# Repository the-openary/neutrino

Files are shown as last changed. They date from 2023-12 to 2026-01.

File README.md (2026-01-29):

# Neutrino

### Overview

This is Neutrino! It's a portable 3D printer that is meant to be cheap and accessible - it fits inside a filament box! ~~Currently in development~~ currently unfinished, do NOT try building your own without messaging me for help for now. Join the the Discord server [here!](https://discord.gg/VZFWGp7FHZ). Made by @qcoral

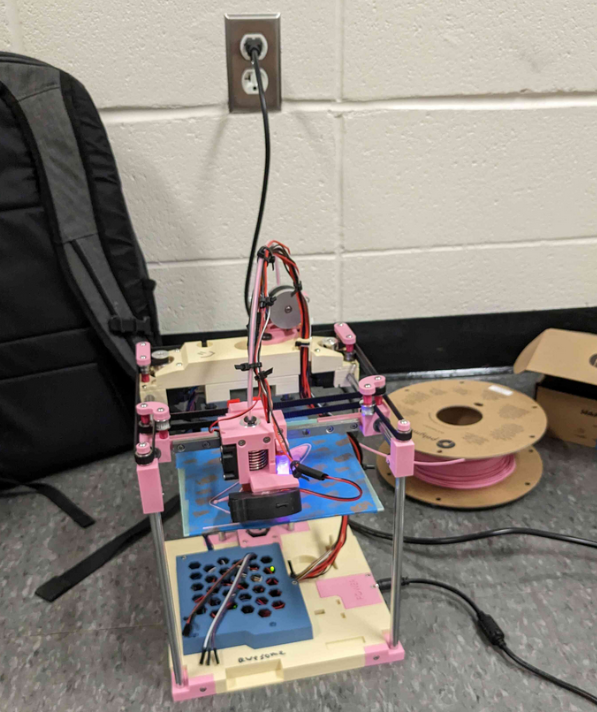
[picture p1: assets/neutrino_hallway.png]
Picture of Neutrino in a hallway


The `dev_process` folder contains a selection of notes & data that provide a peek into the development process of this printer. Due to privacy reasons it is only a snippet. If there's something specific feel free to reach out. 

### Features
- Fits in a 200x200x70mm volume
- Under $300 CAD (using the attached BOM)
- Uses common, off-the-shelf parts
- Mostly self replicating

*currently the base cannot be self-printed

## 2025-12-12 Update:

I last updated this printer almost 2 years ago in 2024. The printer works, but the useability could definitely be improved.

While I would love to someday really put in the polish to properly finish this design, I really am not sure when that would be. Many of the parts would have to be redesigned from scratch, and I've recently been enjoying other projects much more. That being said, this was still an absolute blast to work on!

Feel free to fork this if you so desire. All I ask is that you give proper attribution!

---
### Getting started

In the root of the repository is a file called `BOM.xlsx`. Contains all the relevant links, notes, etc. Currently missing screw counts, please use the CAD for that!

Join the discord for help, I will gladly give guidance on how to build your own.

---
### FAQ:

**Can I see a video?**

There are short clips that can be found in the discord. Currently working on a proper release video, will try and get that out soon<sup>tm</sup>.

**Where's the extruder?**

Great question! Neutrino is designed to use a Sherpa Mini in bowden configuration. Due to copyright, it cannot be included in the CAD. It can be found [here](https://github.com/Annex-Engineering/Sherpa_Mini-Extruder). Totally awesome design.

**Why a Bowden Setup?**

Initially the printer had a Direct Drive setup, but this was later swapped to Bowden. There were a couple reasons for this
- Faster printing
- Short tube length
- Easier maintenance
- Easier to explain to others
    - Being a portable printer, many people who have never seen a 3D printer see it. I think this makes Neutrino double as an educational/inspirational tool and for that reason it is easier to explain the separate parts of a Bowden extruder vs a DD setup. 

**Where can I source my parts?**

Anywhere you can find them. The `BOM.xlsx` file contains links to all the sources that I used during development. The printer itself uses all standard 8mm + M3 hardware. Use AliExpress, Amazon, spare parts, etc. Unfortunately you will need to print your own parts for now, but that will change soon.

**Is there an assembly guide?**

Not yet, working on that soon. For now you should just use the CAD. There is also the [discord](https://discord.gg/VZFWGp7FHZ) for help. I can assist you personally there.

**What is under `OLED_Module`?**

Under OLED_Module is a custom, optional PCB that contains an OLED display, rotary encoder, kill switch, and speaker. The case is still WIP, but the PCB itself has been tested and works well.

**Why the name "Neutrino"?**

The [Positron](https://github.com/KRALYN/PositronV3) project was a huge inspiration for me whilst designing this project. Seeing the innovation process and Kralyn's willingness to tackle problems was a huge motivator for me. While Neutrino was originally a codename, I believe it fits pretty well. 

---

### TODO:

- [ ] Make the base self replicating
- [ ] Misc clearance fixes
- [ ] Add pin breakout connector
- [ ] Add PET Recycling integration

#### [Credits](/CREDITS.md)

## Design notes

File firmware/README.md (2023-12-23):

## Firmware Configuration

ESP8266 & Klipper firmware for Neutrino

In the esp8266 folder there is a precompiled hex file for the Wemos D1 Mini. The credentials are preconfigured to the following:
- SSID: esp@neutrino
- Password: secretpi

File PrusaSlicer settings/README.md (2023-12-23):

# PrusaSlicer Settings

Config files for PrusaSlicer. Currently contains the printer settings and profiles for:

Layer heights:
- 0.3mm
- 0.2mm

Filaments:
- PLA

More to be added soon. Currently one large file, working on separating each profile so you can import only what you need. Refer to [PrusaSlicer Documentation](https://help.prusa3d.com/article/how-to-import-and-export-custom-profiles-in-prusaslicer_382766) for help.

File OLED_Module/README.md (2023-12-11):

Custom OLED Module for the Neutrino

Pinout for SKR Mini E3 V2.0

```
 *            SKR Mini E3 V2.0
 *                 ------
 * (NONE)    PB5  | 1  2 | PA15 (BTN_ENC)
 * (BTN_EN1) PA9  | 3  4 | RESET
 * (BTN_EN2) PA10   5  6 | PB9  (SDA)
 * (SCL)     PB8  | 7  8 | PB15 (BEEPER)
 *            GND | 9 10 | 5V
 *                 ------
 *                  EXP1
 ```
Source: https://upload.wikimedia.org/wikipedia/commons/9/90/Stm32f103_pinout_diagram.png

Editing Marlin: 
- Add the following to `pins_BTT_SKR_MINI_E3_common.h` under  `#elif HAS_WIRED_LCD`
```C
  #elif ENABLED(OLED_PANEL_TINYBOY2)

    #define BEEPER_PIN EXP1_08_PIN //PB15

    #define BTN_ENC EXP1_02_PIN //PA15
    #define BTN_EN1 EXP1_03_PIN //PA9
    #define BTN_EN2 EXP1_05_PIN //PA10
```
- Then select 
```C 
#define OLED_PANEL_TINYBOY2
``` 
Under the `OLED Displays` section of `configuration.h` (roughly line 2980)

Special thanks to czupryna011 for the instructable I based this off of https://www.instructables.com/Small-and-Cheap-Tiny-OLED-for-Ender-3-stock-and-SK/

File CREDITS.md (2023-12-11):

# Credits

The CAD model uses the following models as placeholders for now:

- [Raspberry Pi Zero W](https://grabcad.com/library/raspberry-zero-1)
- [BLTouch](https://grabcad.com/library/bltouch-v3-1-1)
- [Lolin D1 Mini](https://grabcad.com/library/wemos-esp8266-lolin-d1-mini-v4-1)
- As well as an SKR Mini & E3D v6 from the VORON Project 3D printer CAD files

These models were very useful during the design process off the printer, particularly when mapping out locations of the different parts. These will be replaced by custom-made models in the future, but for now these models are used

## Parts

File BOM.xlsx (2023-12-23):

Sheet: Main Parts
Item | Quantity | Main Price | Alt. Price | Link | Notes | Alternative source | Alternate source 2
KINEMATICS
STEPPERONLINE NEMA 17 20mm motor 3pcs | 1 | $41.47 |  | https://www.aliexpress.com/item/1005003226027617.html | Alternative source has JST connectors | https://www.aliexpress.com/item/1005004708155105.html | https://www.aliexpress.com/item/32585429251.html
MGN9C Linear Rail 150mm (LYXCNC) | 1 | $10.14 |  | https://www.aliexpress.com/item/1005004519572683.html
4pcs 8x150mm linear rod (ZHUHAI) | 1 | $14.06 |  | https://www.aliexpress.com/item/1005001813564948.html | For Z axis, you can optionally do 200mm. Make sure to change leadscrew accordingly!
2pcs 8x150mm linear rod (ZHUHAI) [Y Axis] | 1 | $8.48 |  | https://www.aliexpress.com/item/1005001585997299.html | For Y axis, do not change!
2PCs LM8SUU (SUPER3D) | 1 | $2.91 |  | https://www.aliexpress.com/item/32819163985.html
1PCs LM8UU (SUPER3D) | 2 | $3.52 |  | https://www.aliexpress.com/item/4000528511830.html
GT2 2GT Open Belt 3m (POWGE) | 1 | $8.45 |  | https://www.aliexpress.com/item/902692789.html
1pcs 150mm 2mm pitch 8mm leadscrew (ZHUHAI) | 1 | $6.55 |  | https://www.aliexpress.com/item/32873975375.html | Alternate source $3.67 | https://www.aliexpress.com/item/4001332632943.html
10pcs F623ZZ Bearing (AXK HARDWARE) | 2 | $9.48 |  | https://www.aliexpress.com/item/1005002679059125.html | Alternate source is roughly $15, RS. Can use toothed idler pulleys, we just need 12 "Joints" total. | https://www.aliexpress.com/item/1005004095001000.html
1pcs GT2 2GT 5MM Bore Timing pulley (POWGE) | 2 | $7.05 |  | https://www.aliexpress.com/item/32995102911.html | Alternate source is roughly $2.34, quality could be suspect | https://www.aliexpress.com/item/1005002226516848.html
2pcs GT2 3MM Bore 16T Idler timing pulley (Maecoom) | 1 | $3.34 |  | https://www.aliexpress.com/item/1005003291106065.html | Powge as alternate source | https://www.aliexpress.com/item/32736106347.html
Flexible Clamp Coupler (BTT) | 1 | $3.34 |  | https://www.aliexpress.com/item/32875353222.html | This part really should only be $1, just testing this type | https://aliexpress.com/item/4000275512446.html
TOTAL KINEMATICS |  | $118.79
ELECTRONICS
BTT SKR Mini E3 | 1 | $36.57 |  | https://aliexpress.com/item/4001050254672.html
Wemos S2 Mini (AITEXM ROBOT) | 1 | $4.19 |  | https://www.aliexpress.com/item/1005003763905349.html | Optional, could just control via PC. Alternate souce has a lot more orders | https://www.aliexpress.com/item/1005001621784437.html
OLED Display Upgrade (See other page) | 1 | $17.84 |  |  | Optional Upgrade
24v 8A PSU | 1 | $25.99 |  | https://www.amazon.ca/Adapter-100-240V-Converter-Transformer-Connector/dp/B0B1D18JMX/ | Can use other ones as well, this one works best for me
5pcs Rocker switch | 1 | $2.28 |  | https://www.aliexpress.com/item/1005004733281102.html
TOTAL ELECTRONICS |  | $86.87
TOOLHEAD
Mellow V6 Hotend | 1 | $22.59 |  | https://aliexpress.com/item/33040074653.html?
Sherpa Micro | 1 | $33.52 |  | Check other sheet
5015 Cooling Fan (Maecoom) | 1 | $1.81 |  | https://www.aliexpress.com/item/1005003284761769.html | $2.61 from BTT | https://www.aliexpress.com/item/32509279837.html
BLTouch (Wavgat) | 1 | $11.13 | $18.02 | https://www.aliexpress.com/item/1005004501631131.html | Alternate source is $11.13. Not needed if we're using an inductive | https://www.aliexpress.com/item/32840691571.html
TOTAL HOTEND |  | $69.05
BED
150x150mm FR4 Sheet 1.5mm (BUYNOW) | 1 | $9.11 |  | https://www.aliexpress.com/item/1005004784813257.html | Not needed with alu bed
TOTAL BED |  | $9.11
FASTENERS
M3x5x4 Heatset inserts (100pcs) | 1 | $7.73 |  | https://www.aliexpress.com/item/4000232858343.html
50pcs M3 Washers (6mm OD 0.5mm thick) | 1 | $3.42 |  | https://www.aliexpress.com/item/32917948919.html
M3 Square nuts | 1 |  |  | https://www.aliexpress.com/item/1005002179121598.html
M3x8 SHCS | 4
M3x12 BHCS
M3x16 SHCS | 2
M3x20 BHCS | 2
M3x25 BHCS | 4
M3x30 BHCS | 8
Neodymium magnets 20pcs 6x3mm | 1 | $3.80 |  | https://www.aliexpress.com/item/1005005118080851.html
TOTAL FASTENERS |  | $11.15
TOTAL (MINIMUM) |  | $267.94
TOTAL (RECOMMENDED) |  | $294.97

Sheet: Budget Sherpa Mini
Item | Quantity | Main Price | Alt. Price | Link | Notes | Alternative source
2 pcs 3x20mm shaft | 1 |  | $2.44 | https://www.aliexpress.com/item/32945448142.html | Completely optional with fixed idler mod. Highly recommend it.
BMG Internals w/ hardened gear | 1 | $8.00 |  | https://www.aliexpress.com/item/1005003334389217.html | I recommend the Trianglelabs kit, however it is much more expensive
NEMA 14 36mm pinion pancake motor (SIBOOR) | 1 | $17.65 |  | https://www.aliexpress.com/item/1005004096324389.html |  | https://www.aliexpress.com/item/1005004843857269.html | https://www.aliexpress.com/item/1005005215303623.html
M5x7x0.5mm Washer 50pcs (Cheng da) | 1 | $2.05 |  | https://www.aliexpress.com/item/33043019654.html |  | https://www.aliexpress.com/item/1005002046188859.html
Heatset inserts - M3x5x4 | 4 |  |  | https://www.aliexpress.com/item/4000232858343.html | Use the ones you bought with the printer
M3x20 BHCS Screw | 1 |  |  | JIANKUI | Use the ones you bought with the printer
M3x16 BHCS Screw | 2 |  |  | JIANKUI | Use the ones you bought with the printer
M3x8 BHCS Screw | 2 |  |  | JIANKUI | Use the ones you bought with the printer
BMG Shaft Assembly (Trianglelab) |  | $5.82 |  | https://www.aliexpress.com/item/32946823004.html | REQUIRED IF YOU DO NOT GRIND DOWN THE SHAFT IN OTHER KITS
TOTAL |  | $33.52

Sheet: Neutrino Display
Item | Quantity | Main Price | Alt. Price | Link | Notes | Alternative source
0.96" i2c OLED display (SAMIORE) | 1 | $3.57 |  | https://www.aliexpress.com/item/32638662748.html | Get single colour
5pcs 15mm Plum handle EC11 Encoder (Excellence electronic) | 1 | $2.40 |  | https://www.aliexpress.com/item/1005003824684681.html
10pcs 10 pin male right angle IDC connector (IC Components Store) | 1 | $2.36 |  | https://www.aliexpress.com/item/32955520296.html |  | https://www.aliexpress.com/item/1005004268331255.html
1pcs 10 Pin IDC Cable 10cm (excellence electronic) | 1 | $1.18 |  | https://www.aliexpress.com/item/1005003057058334.html
5pcs display PCB (JLCPCB or manufacturer of your choice) | 1 | $3.50
5pcs 5V Active Buzzer (ESTARDYN) | 1 | $2.69 |  | https://www.aliexpress.com/item/1005004207766097.html | You can omit this
Shipping |  | $2.14 |  |  | Excellence electronic ships everything for a flat price
Total |  | $17.84

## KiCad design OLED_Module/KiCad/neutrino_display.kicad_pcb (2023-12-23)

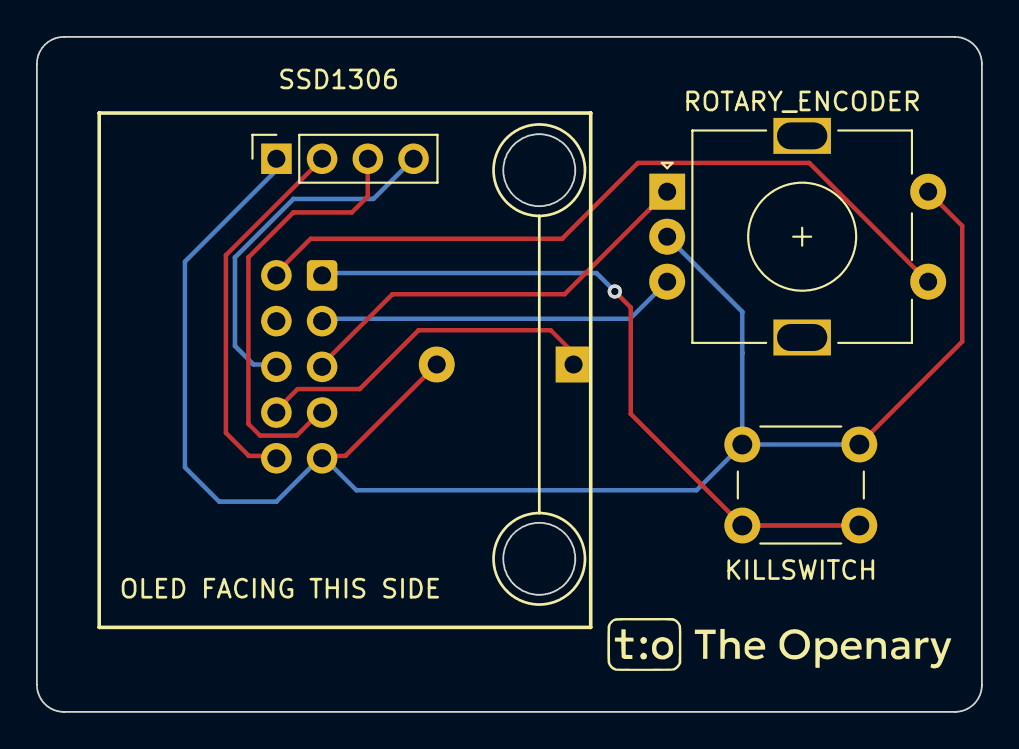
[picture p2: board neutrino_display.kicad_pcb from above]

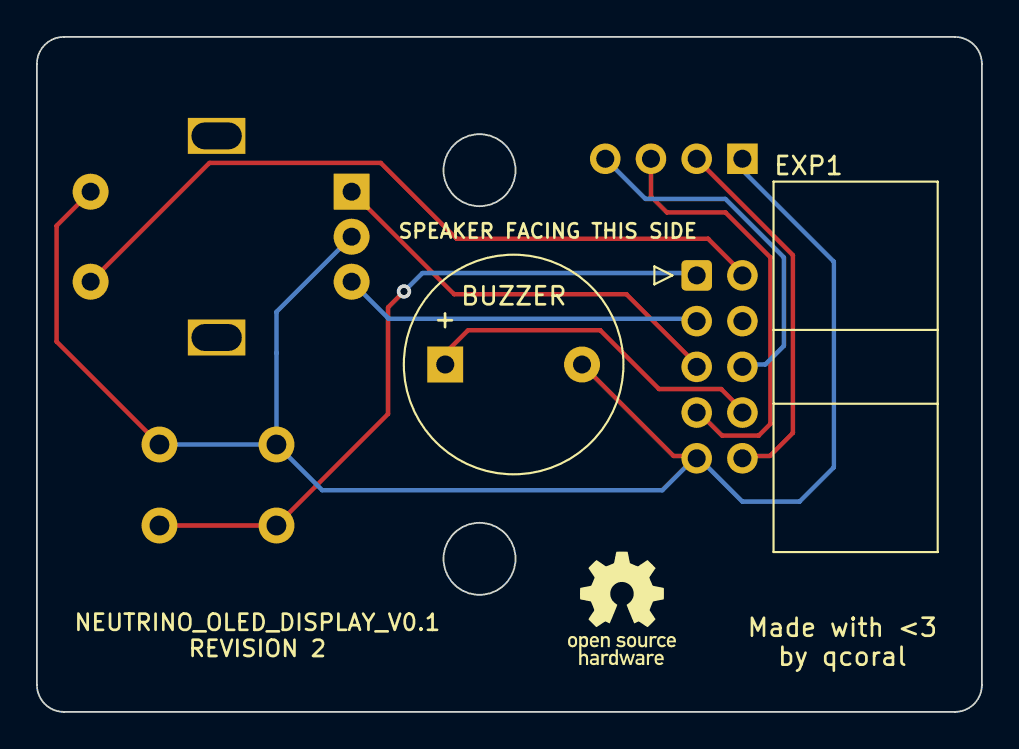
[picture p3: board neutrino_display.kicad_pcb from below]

Board: 2 copper layers, 52.5 x 37.5 mm, 5 parts (2 on the bottom side), 9 nets.

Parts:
BUZZER: Buzzer; Buzzer_12x9.5RM7.6
EXP1: 2x5; IDC-Header_2x05_P2.54mm_Horizontal
J2: OLED_Headers; PinSocket_1x04_P2.54mm_Vertical
KILLSWITCH: Kill Switch; SW_PUSH_6mm_H8.5mm
ROTARY_ENCODER: EC11_Switch; RotaryEncoder_Alps_EC11E-Switch_Vertical_H20mm

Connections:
+5V: EXP1.10, J2.2
BTN_EN1: EXP1.3, ROTARY_ENCODER.B
BTN_EN2: EXP1.5, ROTARY_ENCODER.A
BTN_ENC: EXP1.2, ROTARY_ENCODER.S1
GND: BUZZER.2 (+), EXP1.9, J2.1, KILLSWITCH.2, ROTARY_ENCODER.C, ROTARY_ENCODER.S2
KILLSWITCH: EXP1.1, KILLSWITCH.1
SCL: EXP1.7, J2.3
SDA: EXP1.6, J2.4
SPEAKER: BUZZER.1 (-), EXP1.8

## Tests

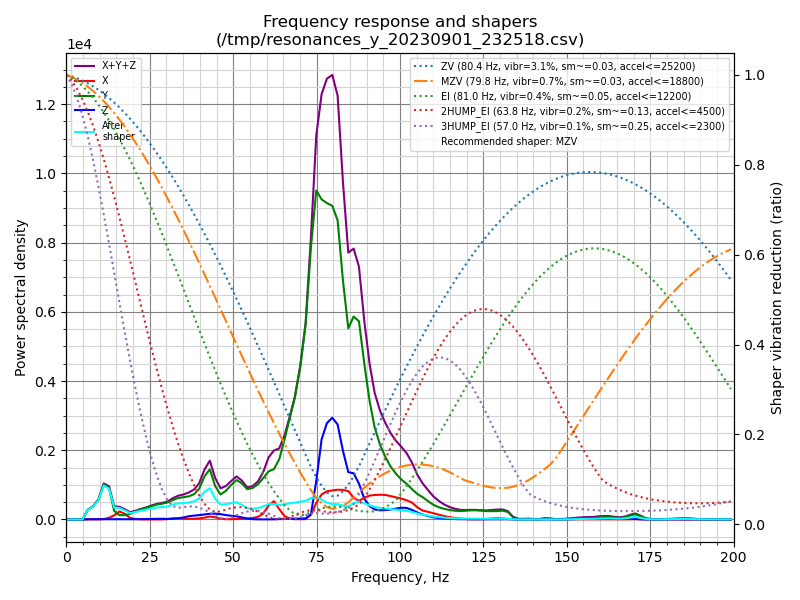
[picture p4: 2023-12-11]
dev_process/Input shaper/shaper_calibrate_y.png

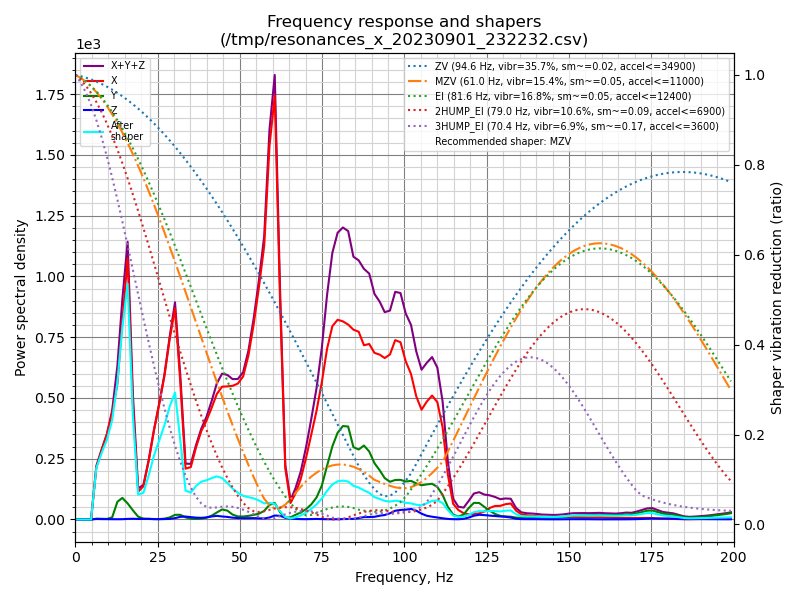
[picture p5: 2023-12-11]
dev_process/Input shaper/shaper_calibrate_x.png

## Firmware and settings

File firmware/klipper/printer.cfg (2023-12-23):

# X and Z are swapped, as well as Y and E. This is to allow for easier wiring
# Refer to klipper documentation when modifying: https://www.klipper3d.org/Config_Reference.html

[include mainsail.cfg]

[mcu]
serial: /dev/ttyAMA0
restart_method: command

[printer]
kinematics: corexy
max_velocity: 400
max_accel: 6000
max_z_velocity: 15
max_z_accel: 300
square_corner_velocity: 6.0

#####################################################################
#      X/Y Stepper Settings
#####################################################################

[stepper_x]
step_pin: PB0
dir_pin: !PC5                                                       # Check motor direction in link above. If inverted, add a ! before PB12
enable_pin: !PB1
rotation_distance: 40
microsteps: 32
full_steps_per_rotation: 200                                        # Set to 400 for 0.9° degree stepper motor, 200 is for 1.8° stepper motors
endstop_pin: tmc2209_stepper_x:virtual_endstop
position_endstop: 0
position_max: 115
homing_speed: 20                                                    # for sensorless homing it is recommended not to go above 40mm/s
homing_retract_dist: 0
homing_positive_dir: false

[tmc2209 stepper_x]
uart_pin: PC11
tx_pin: PC10
uart_address: 1
interpolate: False
run_current: 0.5
# you need to calculate the run_current value using the equation (rated_motor_current * 0.707 = Maximum_run_current) start with a value that is about 60%-70% of your maximum value.
sense_resistor: 0.110
stealthchop_threshold: 0                                            # Set to 999999 to turn stealthchop on, and 0 to use spreadcycle
diag_pin: ^PC2                                                                                                         # YOU NEED TO JUMP THIS DIAG PIN ON YOUR BOARD FOR SENSORLESS HOMING TO WORK
driver_SGTHRS: 32                                                   # this is set to 255 which is the MAX sensitivity for sensorless homing, you will need to tune this later

[stepper_y]
step_pin: PB3
dir_pin: !PB4                                                        # Check motor direction in link above. If inverted, add a ! before PB2
enable_pin: !PD2
rotation_distance: 40
microsteps: 32
full_steps_per_rotation: 200                                        # Set to 400 for 0.9° degree stepper motor, 200 is for 1.8° stepper motors
endstop_pin: tmc2209_stepper_y:virtual_endstop
position_endstop: 115
position_max: 115
homing_speed: 20                                                    # for sensorless homing it is recommended not to go above 40mm/s
homing_retract_dist: 0
homing_positive_dir: true

[tmc2209 stepper_y]
uart_pin: PC11
tx_pin: PC10
uart_address: 3
interpolate: False
run_current: 0.5
# you need to calculate the run_current value using the equation (rated_motor_current * 0.707 = Maximum_run_current) start with a value that is about 60%-70% of your maximum value.
sense_resistor: 0.110
stealthchop_threshold: 0                                            # Set to 999999 to turn stealthchop on, and 0 to use spreadcycle
diag_pin: ^PC15                                                                                                         # YOU NEED TO JUMP THIS DIAG PIN ON YOUR BOARD FOR SENSORLESS HOMING TO WORK
driver_SGTHRS: 25                                                  # this is set to 255 which is the MAX sensitivity for sensorless homing, you will need to tune this later

#####################################################################
#   Z Axis Settings
#####################################################################

[stepper_z]
step_pin: PB13
dir_pin: PB12                                                       # Remove the ! before PB12 if motor direction is inverted.
enable_pin: !PB14
rotation_distance: 8                                                # For T8x8 integrated lead screw
microsteps: 32
endstop_pin: probe:z_virtual_endstop
position_max: 85
position_min: -5
second_homing_speed: 3.0
homing_retract_dist: 3.0

[tmc2209 stepper_z]
uart_pin: PC11
tx_pin: PC10
uart_address: 0
interpolate: False
run_current: 0.5
sense_resistor: 0.110
stealthchop_threshold: 0                                            # Set to 999999 to turn stealthchop on, and 0 to use spreadcycle

[bltouch]
sensor_pin: ^PC14
control_pin: PA1
z_offset: 1.295

[safe_z_home]
home_xy_position: 60, 60
speed: 50.0
z_hop: 10.0
z_hop_speed: 5.0

[bed_mesh]
speed: 120
horizontal_move_z: 5
mesh_min: 10, 10
mesh_max: 100, 100
probe_count: 3, 3

#####################################################################
#   Extrusion & Cooling settings
#####################################################################

[extruder]
step_pin: PB10
dir_pin: PB2                                                        # Add ! if moving opposite direction
enable_pin: !PB11
full_steps_per_rotation: 200                                       # Set to 200 for LDO 1.8° stepper motor, and set to 400 for OMC(StepperOnline) 0.9° stepper motor
rotation_distance: 23.02032                                      # For Sherpa Mini
gear_ratio: 50:10                                                   # For Sherpa Mini
microsteps: 16
nozzle_diameter: 0.600
filament_diameter: 1.750
heater_pin: PC9
## Check what thermistor type you have. See https://www.klipper3d.org/Config_Reference.html#common-thermistors for common thermistor types.
## Use "Generic 3950" for NTC 100k 3950 thermistors
sensor_type: Generic 3950
sensor_pin: PA0
min_temp: 0
max_temp: 260
min_extrude_temp: 0
max_extrude_only_distance: 450
max_extrude_cross_section: 0.8
max_extrude_only_velocity: 75.0
max_extrude_only_accel: 1500
pressure_advance: 0.10                                              # See tuning pressure advance doc
pressure_advance_smooth_time: 0.020



[tmc2209 extruder]
uart_pin: PC11
tx_pin: PC10
uart_address: 2
interpolate: True
## For OMC (StepperOnline) 14HR07-1004VRN 1A 0.9°
#run_current: 0.5   # for OMC 14HR07-1004VRN rated at 1A
## For LDO LDO 36STH17-1004AHG 1A 1.8°
#run_current: 0.3   # for LDO 36STH17-1004AHG
## For LDO LDO 36STH20-1004AHG 1A 1.8°
#run_current: 0.6   # for LDO 36STH20-1004AHG

## For 36HS2418CL16  1.88A (this is a guess)
# run_current: 0.42
run_current: 0.42
sense_resistor: 0.110
stealthchop_threshold: 0                                            # Set to 0 for spreadcycle, avoid using stealthchop on extruder

[heater_fan hotend_fan]
pin: PC6
max_power: 1.0
kick_start_time: 0.5
heater: extruder
heater_temp: 50.0

[fan]
pin: PC7

#####################################################################
#   Extras
#####################################################################

[display]
lcd_type: ssd1306
click_pin: ^!PA15
i2c_bus: i2c1a
encoder_pins: ^PA10, ^PA9
kill_pin: ^!PB5
vcomh: 60

[output_pin beeper]
pin: PB15
value: 0
shutdown_value: 0

#############
# MACROS
#############

[gcode_macro BEEP_NOTIFY]
gcode:
	# Parameters
	{% set i = params.N|default(1)|int %}        ; Iterations (number of times to beep).
	{% set dur = params.DUR|default(100)|int %}  ; Duration/wait of each beep in ms. Default 100ms.

	{% for iteration in range(i|int) %}
		SET_PIN PIN=beeper VALUE=1
		G4 P{dur}
		SET_PIN PIN=beeper VALUE=0
		G4 P{dur}
	{% endfor %}

[gcode_macro LOAD_FILAMENT]
gcode:
	M83                            ; set extruder to relative
	G1 E380 F1600                  ; quickly load filament to down bowden
	G1 E30 F300                    ; slower extrusion for hotend path
	G1 E15 F150                    ; prime nozzle with filament
	G1 E-10 F300                    ; retract a little to prevent oozing
	M82                            ; set extruder to absolute

[gcode_macro UNLOAD_FILAMENT]
gcode:
	M83                            ; set extruder to relative
	G1 E15 F300                    ; extrude a little to soften tip
	G1 E-440 F1600                 ; retract filament completely
	M82                            ; set extruder to absolute

[gcode_macro PRINT_START]
#   Use PRINT_START for the slicer starting script - please customize for your slicer of choice
gcode:
	{% set EXTRUDER = params.EXTRUDER|float %}
	M109 S0
	M117 Homing...
	G28
	M117 Creating Bed Mesh...
	BED_MESH_CALIBRATE
	G0 Z5
	G1 X60 Y60 F3000
	M117 Heating to Printing Temperature...
	M109 S{EXTRUDER}
	#Purge Line Gcode
	BEEP_NOTIFY N=3 DUR=100
	M117 Purging...
	G92 E0            ; set current extruder position to 0
	G90               ; set all axes to absolute
	G0 Z0
	G0 X0 Y0 F6000    ; move axis to near 0,0
	G0 Z0.4           ; lower z
	G91               ; change to relative mode
	G1 X50 E10 F400 ; extrude for 50mm on X
	G1 Y1             ; move Y back 1mm
	G1 X-50 E10 F400; Move back to starting point
	G92 E0            ; set new extruder 0
	G90               ; go back to absolute mode
	M117 Printing...
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

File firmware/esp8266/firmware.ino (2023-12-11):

/*
  ESP8266 firmware for the Neutrino 3D Printer.
*/

#include <ESP8266WiFi.h>
#include <ESP8266mDNS.h>

// Set these to your desired credentials.

#define APSSID "YOUR_SSID_HERE"
#define APPSK "YOUR_PASSWORD_HERE"


const char *ssid = APSSID;
const char *password = APPSK;

void setup() {
  delay(1000);
  Serial.begin(115200);
  Serial.println();
  Serial.print("Configuring access point...");
  WiFi.softAP(ssid, password);
}

void loop() {
  Serial.printf("Stations connected to soft-AP = %d\n", WiFi.softAPgetStationNum());
  delay(500);
}

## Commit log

2023-12-12 updated BOM, README.md
    [BOM.xlsx]
2023-12-23 Fixed PCBs, updated firmware, added PrusaSlicer settings, updated README.md, updated BOM. Awesome :)
    [BOM.xlsx, neutrino_display.kicad_pcb, neutrino_display.kicad_sch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]
